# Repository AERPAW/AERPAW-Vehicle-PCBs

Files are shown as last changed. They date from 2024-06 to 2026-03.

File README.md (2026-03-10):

# vehicle-pcbs

PCB design files for vehicles and accessories used by AERPAW project.

Designs:

- `LAM-original` contains projects (carrier, PDB) for original LAM revisions (<2025)
- `LAM-simplified` contains updated PDB (power distribution board) (>2025)
- `LightBoard` contains design for auxilary LED drivers for SAM revisions
- `SAM4-old` contains projects for original SAM revisions carrier (<2026)
- `SAME` contains projects for updated SAM revisions

Util:

- `kicad-libs` is a unified symbol/footprint library for all projects. Configure future projects to point at this!

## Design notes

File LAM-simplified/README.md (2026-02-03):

# LAM PCBs

This contains various revisions of LAM PDB (power distribution board) PCBs.

`r1.3` is the suggested revision for older LAM hexarotors.

`r2.0` is the suggested revision for newer HAM-based designs, as it supports higher current capacity (at the cost of a different mechanical footprint from 1.X).

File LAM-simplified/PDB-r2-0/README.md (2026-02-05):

# HAM PDBs

This directory contains the KiCad (9.X) project files with design and manufacturing details for the HAM PDB (power distribution board)s.

The PDB ingests raw battery voltage and provides connectors for peripherals to hook into this net.

- 4x 2x3 2.54mm male -- to (original) carrier board
- 2x XT30 -- to aux systems
- 6x XT60 -- to motors
- 2x AS150 -- to batteries (use parallel connection)

The board also has access to a regulated 5V rail from the carrier board.
This net is currently unused, but left in for future revisions that might make use of it.

## Manufacturing

The `jlcpcb` directory and `jlcpcb.zip` contains manufacturing files that can be directly uploaded to JLCPCB's website.
A handful of settings should be changed: pick a copper weight >= 3oz, and as high of a temperature substrate as available.
The below screenshot shows an example order that should be reasonable for this application.

Screenshot 2026-02-05 at 13-56-46 Online PCB Instant Quote - JLCPCB

Assembly of this board is simple: just solder through-hole connectors into their appropriate slots.
Do not directly solder wires into this PCB.
Every connection must be made through a connector to ensure that all current expectations on wires/connectors are upheld.

When mechanically attaching this board inside the drone chassis, use brass standoffs.
The board, by design, exposes the GND net to all mechanical mounting holes.
This *should* aid with grounding the drone's chassis dependent on the rest of the mechanical design.

## BOM

A BOM can be assembled by looking at the LCSC field.
Each part number can be searched on LCSC to get ordering information and/or search terms to find similar parts.
LCSC is preferred in this case because they are the only major parts provider sourcing the needed AMASS connectors, and their system is tightly integrated with JLC.

- [2x XT30-F](https://www.lcsc.com/product-detail/C2913282.html)
- [6x XT60-F](https://www.lcsc.com/product-detail/C428722.html)
- [2x AS150UPW-M](https://www.lcsc.com/product-detail/C19268054.html)
- ?x standard 2.54mm pin headers
- [3x Keystone 5010 test points (optional)](https://www.lcsc.com/product-detail/C2906765.html)

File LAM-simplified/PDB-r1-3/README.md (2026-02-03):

# "EASYLAM" PDB (revision 1.3)

This directory contains the KiCad (9.X) project files with design and manufacturing details for the simplified LAM PDB (power distribution board)s.

The PDB ingests raw battery voltage and provides connectors for peripherals to hook into this net.

- 4x 2x3 2.54mm male -- to carrier board
- 2x XT30 -- to aux systems
- 6x XT60 -- to motors
- 2x XT90 -- to batteries (use parallel connection to batteries)

There isn't a strict upper limit on the current that our drones might demand, but this board is fairly conservatively designed to help move failure points to offboard connectors.

The board also has access to a regulated 5V rail from the carrier board.
This net is currently unused, but left in for future revisions that might make use of it.

## Manufacturing

The `jlcpcb` directory contains manufacturing files that can be directly uploaded to JLCPCB's website.
A handful of settings should be changed, documented below:

- screenshot TODO, but we want to pick the heaviest copper weight available and an appropriate process for exposed pads (ENIG?)

Assembly of this board is simple: just solder through-hole connectors into their appropriate slots.
Do not directly solder wires into this PCB.
Every connection must be made through a connector to ensure that all current expectations on wires/connectors are upheld.

When mechanically attaching this board inside the drone chassis, use brass standoffs.
The board, by design, exposes the GND net to all mechanical mounting holes.
This *should* aid with grounding the drone's chassis dependent on the rest of the mechanical design.

## BOM

A BOM can be assembled by looking at the LCSC field.
Each part number can be searched on LCSC to get ordering information and/or search terms to find similar parts.
LCSC is preferred in this case because they are the only major parts provider sourcing the needed AMASS connectors, and their system is tightly integrated with JLC.

For simplicity, a BOM is below:

- [2x XT30-F](https://www.lcsc.com/product-detail/C2913282.html)
- [6x XT60-F](https://www.lcsc.com/product-detail/C428722.html)
- [2x XT90-F](https://www.lcsc.com/product-detail/C3040690.html)
- ?x standard 2.54mm pin headers
- [3x Keystone 5010 test points (optional)](https://www.lcsc.com/product-detail/C2906765.html)

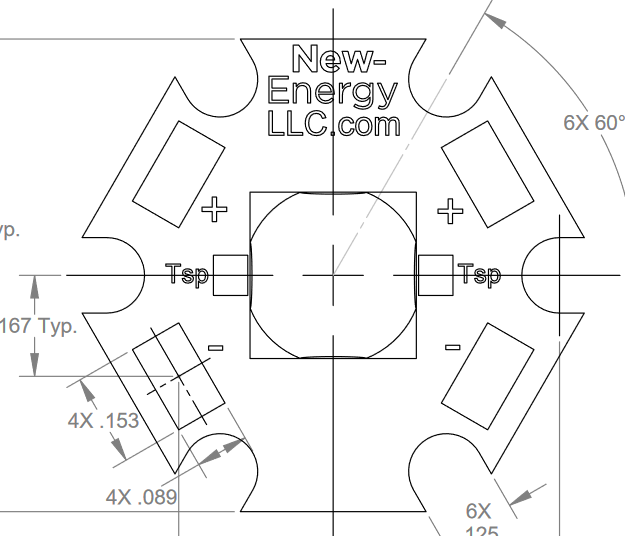
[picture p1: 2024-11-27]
LightBoard/starboard_profile.png

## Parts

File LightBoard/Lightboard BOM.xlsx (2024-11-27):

Reference | Part | Footprint | Qty | Link | Price (1) | Price (total) | Misc
C1 | Cap 0.1u | 1206 | 1 | https://www.digikey.com/en/products/detail/vishay-sprague/293D104X9035A2TE3/1559461 | $0.43 | $0.43 | Decoupling (tantalum)
J1, J2 | JST_EH 2x2.5mm Male Horiz |  | 2 | https://www.digikey.com/en/products/detail/jst-sales-america-inc/S2B-EH/926533?0=%2Fheaders-male-pins | $0.12 | $0.24 | Rated for 3A
R1, R2, R4, R5, R8 | Res 10k | 1206 | 5 | https://www.digikey.com/en/products/detail/yageo/RC1206FR-0710KL/728483 | $0.10 | $0.50
R3 | Res 0.22 1% | 1206 | 1 | https://www.digikey.com/en/products/detail/eaton-electronics-division/MFHA1206R2200FC/16713417 | $0.34 | $0.34 | Current tuning
R6 | Res 80k | 1206 | 1 | https://www.digikey.com/en/products/detail/yageo/RC1206FR-0780K6L/729126 | $0.10 | $0.75
R7 | Res 35 0.5W | 1206 | 1 | https://www.digikey.com/en/products/detail/yageo/SR1206JR-7T36RL/9696427 | $0.75 | $0.75 | Power shunt (optional)
U1 | IS32LT3140A | 14-TSSOP | 1 | https://www.digikey.com/en/products/detail/lumissil-microsystems/IS32LT3140A-ZLA3-TR/15194878 | $2.00 | $2.00 | LED Driver
Heat Sink |  |  | 1 | https://www.digikey.com/en/products/detail/sparkfun-electronics/PRT-18704/21443080 | $2.44 | $2.44 | Optional
M3 Standoff |  |  | 6 | https://www.digikey.com/en/products/detail/keystone-electronics/24339/1532140 | $0.91 | $5.46
PCB |  |  | 1 |  | $0.40 | $0.40 | JLCPCB
 |  |  |  |  |  | $13.31

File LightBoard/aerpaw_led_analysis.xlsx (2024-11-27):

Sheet: Sheet1
LED | Link | Color | Brightness (lm/W) | Brightness (80%) | V_f | Current (max) | Power (80%) | Price | Power (80%) | Brightness (80%)
MHBBWT | https://www.digikey.com/en/products/detail/new-energy/MHBBWT-0000-000C0BE265E-SB01/6817726 | 6500K | 146 | 715.4 | 8.75 | 0.7 | 4.9 | 6.24 | 4.9 | 715.4
BXRC-40C1001 | https://www.digikey.com/en/products/detail/bridgelux/BXRC-40C1001-C-83/15520071 | 4000K | 192 | 4715.52 | 30.7 | 1 | 24.56 | 7.1 | 24.56 | 4715.52
BXRC-40E1000 | https://www.digikey.com/en/products/detail/bridgelux/BXRC-40E1000-D-83/12313698 | 4000K | 182 | 3625.44 | 24.9 | 1 | 19.92 | 4.78 | 19.92 | 3625.44
XHP70B | https://www.digikey.com/en/products/detail/new-energy/XHP70B-00-0000-0D0BP250E-SB01/7428211 | 5000k | 151 | 3479.04 | 12 | 2.4 | 23.04 | 20.5 | 23.04 | 3479.04
LZ4-40C | https://www.digikey.com/en/products/detail/ams-osram-usa-inc/LZ4-40CW08-0065/4970100 | 6500K | 101 | 1018.08 | 12.6 | 1 | 10.08 | 16.5 | 10.08 | 1018.08
MHBBWT-0000 | https://www.digikey.com/en/products/detail/new-energy/MHBBWT-0000-000C0HC427G-SB01/6817724 | 2700K | 117 | 573.3 | 8.75 | 0.7 | 4.9 | 6.69 | 4.9 | 573.3
LST1-01 | https://www.digikey.com/en/products/detail/new-energy/LST1-01C54-5765-01/16679676 | 5700K | 116 | 1108.032 | 3.98 | 3 | 9.552 | 10.24 | 9.552 | 1108.032
LST1-01G03 | https://www.digikey.com/en/products/detail/new-energy/LST1-01G03-5070-01/9816713 | 5000K | 114 | 902.88 | 3.3 | 3 | 7.92 | 4.28 | 7.92 | 902.88
 |  |  |  |  |  |  |  |  | 8 | 520
 |  |  |  |  |  |  |  |  | 1.68 | 82.32
LZ4-40R108-0000 | https://www.digikey.com/en/products/detail/ams-osram-usa-inc/LZ4-40R108-0000/4976731 | red | 65 | 520 | 10 | 1 | 8 | 13.91 | 2.706 | 365.31
LST1-01H06-RED1-01 | https://www.digikey.com/en/products/detail/new-energy/LST1-01H06-RED1-01/10663117 | red | 49 | 82.32 | 2 | 1.05 | 1.68 | 4.22
 |  |  |  |  |  |  |  |  | 2.562 | 299.754
LST1-01H06-LME1-01 | https://www.digikey.com/en/products/detail/new-energy/LST1-01H06-LME1-01/10663113 | lime | 135 | 365.31 | 2.75 | 1.23 | 2.706 | 5.72
LST1-01H07-GRN1-01 | https://www.digikey.com/en/products/detail/new-energy/LST1-01H07-GRN1-01/10663119 | green | 117 | 299.754 | 3.05 | 1.05 | 2.562 | 4.22

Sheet: bom
3mm standoffs
jst-eh headers (2 pin)

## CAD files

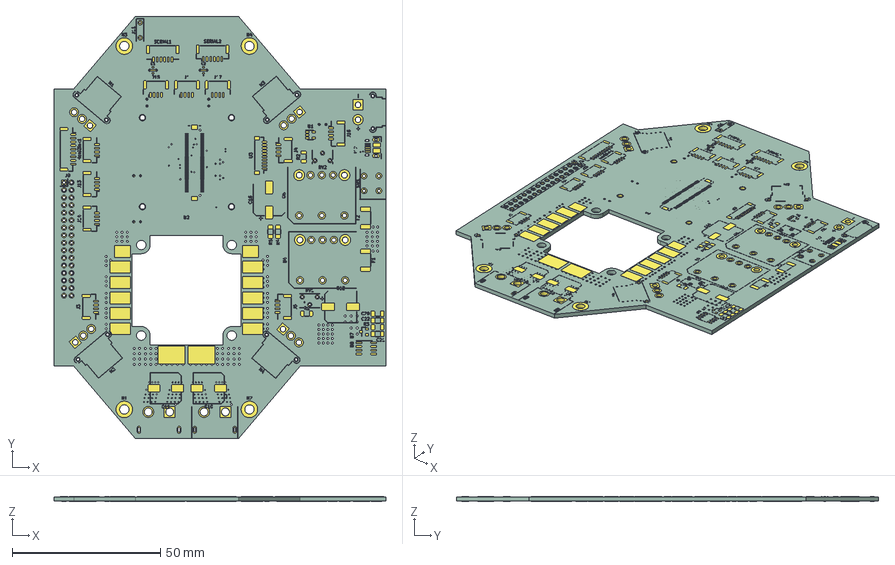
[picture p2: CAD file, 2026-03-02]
SAM-original/SAM4_Mainboard.step
111.7 x 142.2 x 1.66 mm
SAM4_Mainboard_pad
SAM4_Mainboard_silkscreen x 2
SAM4_Mainboard_PCB

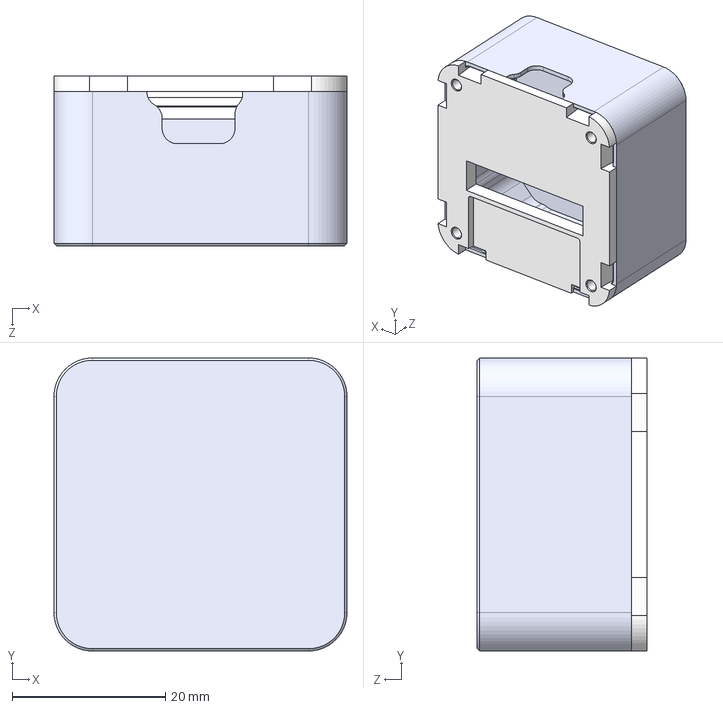
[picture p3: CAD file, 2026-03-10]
kicad-libs/3d/Cube.STEP
38.2 x 38.2 x 22.1 mm
cubemini_base_v1_20180513.stp
std_cube_lid_h20-1mm_20180816.stp

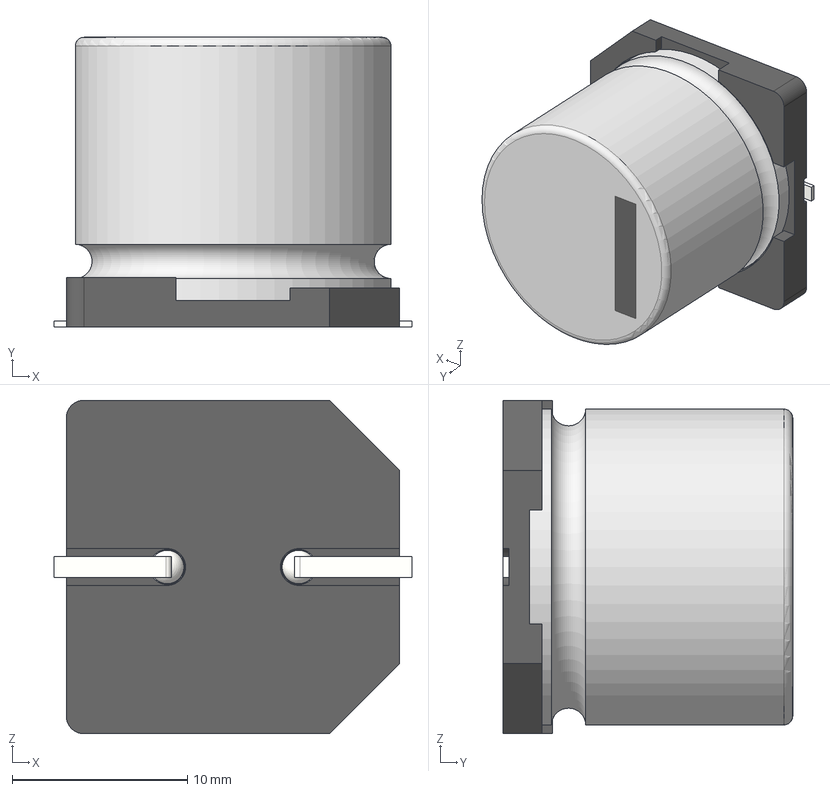
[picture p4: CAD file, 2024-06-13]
LAM-original/P2_PowerSystem/18 SIZE CODE K16.stp
20.4 x 16.5 x 19.0 mm
標準品ケースΦ18x15L SIDE CODE K1 6
標準品座版Φ18 SIZE CODE K16
標準品リード線Φ18 SIZE CODE K1 6 x 2

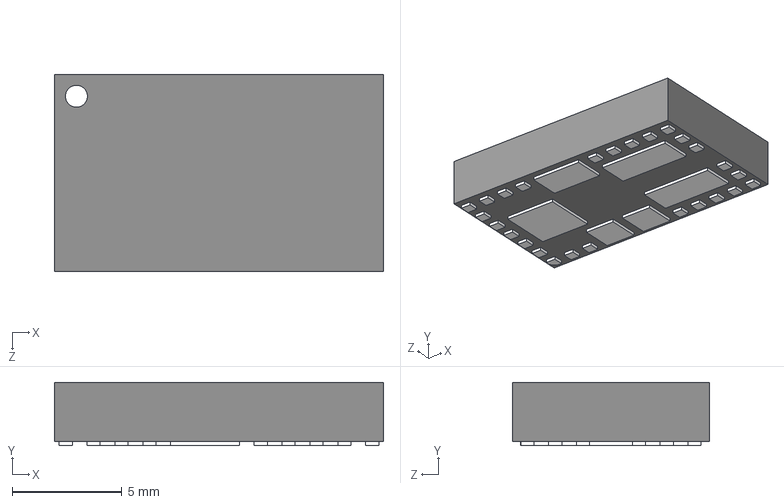
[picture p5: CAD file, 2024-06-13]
LAM-original/P2_PowerSystem/2020-09-24_06-53-47/21-0879B_L32915+3.STEP
15.0 x 2.88 x 9.00 mm

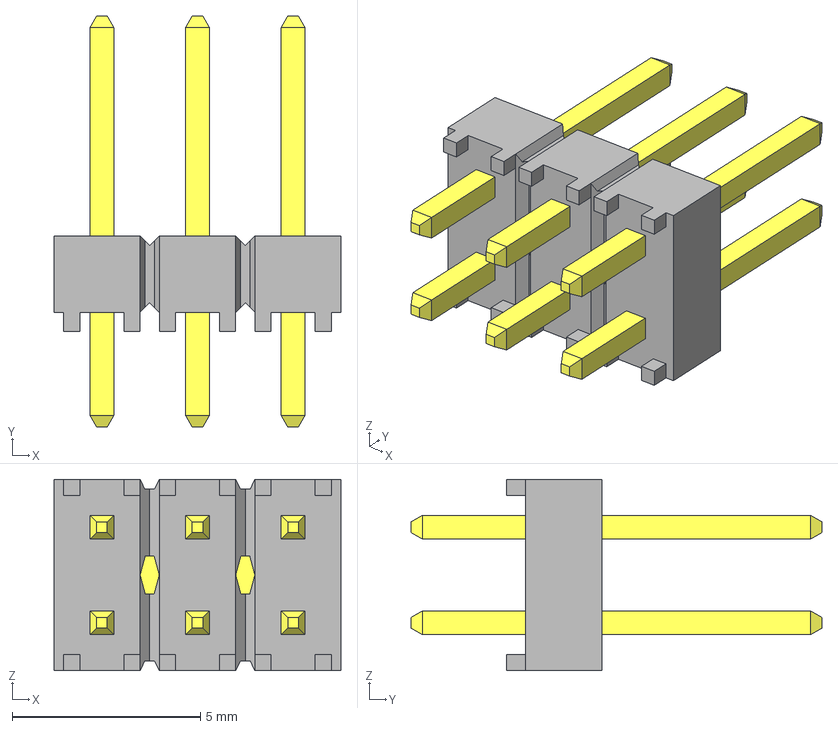
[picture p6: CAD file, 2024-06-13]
LAM-original/P2_PowerSystem/PDB/TSW-103-07-F-D.stp
7.62 x 10.9 x 5.08 mm
_TSW-103-07-F-D_body
_T-1S6-07-TSW-1-07-3-D

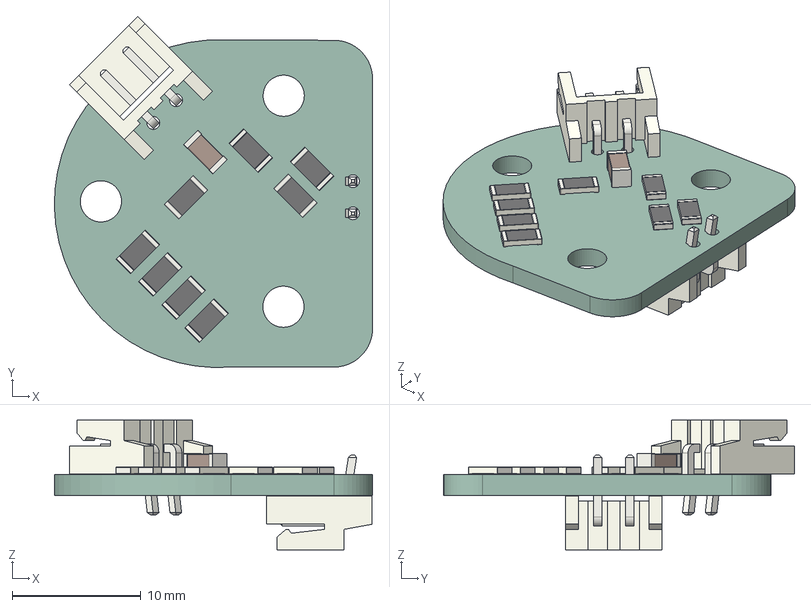
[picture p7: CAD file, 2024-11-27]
LightBoard/lightboard/lightboard.step
24.7 x 27.3 x 10.1 mm
R_1206_3216Metric x 8
JST_S2B_EH x 2
C_1206_3216Metric
lightboard_PCB

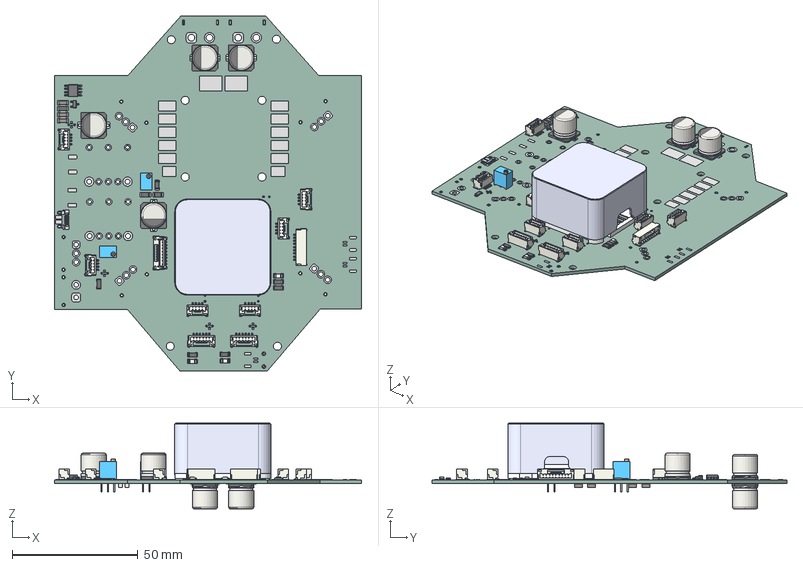
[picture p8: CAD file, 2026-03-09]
SAM-original/sam4_r1.2.step
122.0 x 141.0 x 34.1 mm
R_1206_3216Metric x 9
JST_GH_SM09B-GHS-TB_1x09-1MP_P1.25mm_Horizontal
CP_Elec_10x10 x 4
C_1206_3216Metric x 11
SOIC-8_3.9x4.9mm_P1.27mm
JST_GH_BM04B-GHS-TBT_1x04-1MP_P1.25mm_Vertical x 6
CP_Elec_10x10.5 x 2
JST_SH_BM10B-SRSS-TB_1x10-1MP_P1.00mm_Vertical
LED_1206_3216Metric x 3
Potentiometer_Bourns_3266W_Vertical x 2
JST_GH_BM08B-GHS-TBT_1x08-1MP_P1.25mm_Vertical
JST_GH_BM06B-GHS-TBT_1x06-1MP_P1.25mm_Vertical x 2
SOT-23
cubemini_base_v1_20180513.stp
std_cube_lid_h20-1mm_20180816.stp
sam4_pad
sam4_PCB

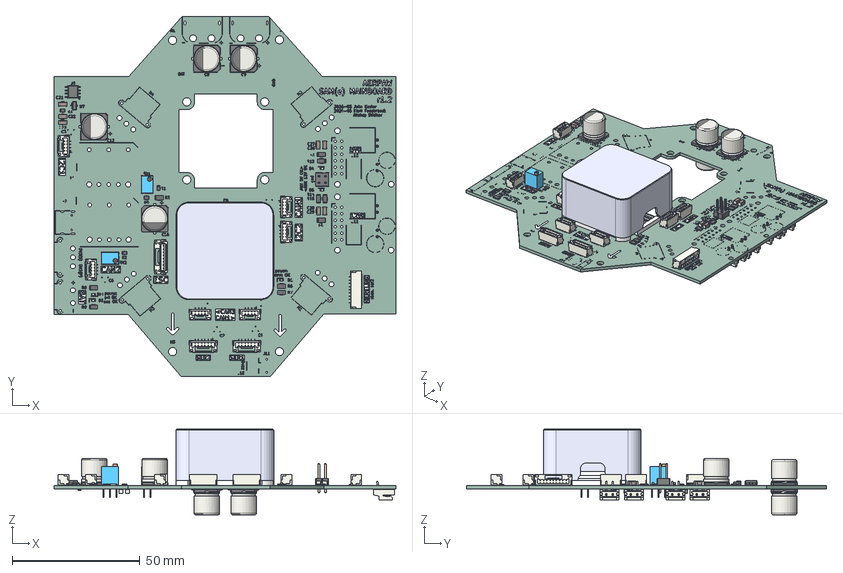
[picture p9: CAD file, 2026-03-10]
SAME/sam4/sam4.step
133.8 x 141.0 x 33.6 mm
LED_0603_1608Metric x 5
R_0805_2012Metric x 6
JST_GH_SM09B-GHS-TB_1x09-1MP_P1.25mm_Horizontal
CP_Elec_10x10 x 4
R_1206_3216Metric x 8
C_1206_3216Metric x 15
Fuse_1206_3216Metric x 2
SOIC-8_3.9x4.9mm_P1.27mm
JST_GH_BM04B-GHS-TBT_1x04-1MP_P1.25mm_Vertical x 6
CP_Elec_10x10.5 x 2
JST_SH_BM10B-SRSS-TB_1x10-1MP_P1.00mm_Vertical
PinHeader_2x02_P2.54mm_Vertical
Potentiometer_Bourns_3266W_Vertical x 2
JST_GH_BM08B-GHS-TBT_1x08-1MP_P1.25mm_Vertical
JST_GH_BM06B-GHS-TBT_1x06-1MP_P1.25mm_Vertical x 2
SOT-23
cubemini_base_v1_20180513.stp
std_cube_lid_h20-1mm_20180816.stp
JST_EH_S2B-EH_1x02_P2.50mm_Horizontal x 4
sam4_silkscreen x 2
sam4_PCB

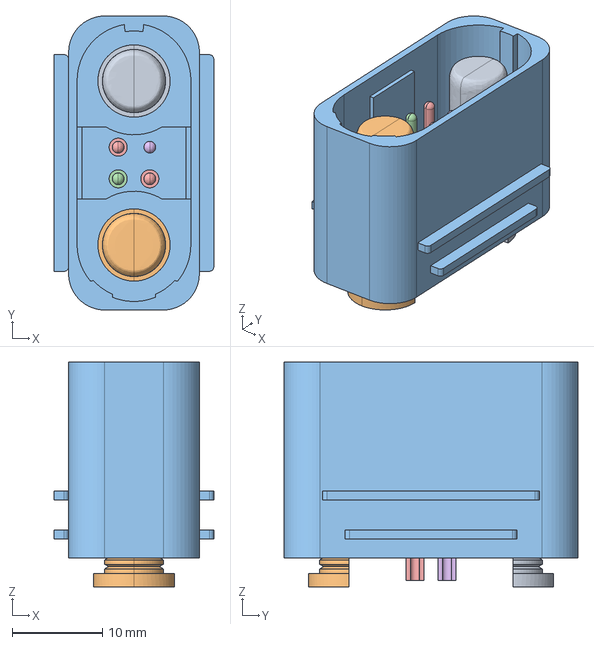
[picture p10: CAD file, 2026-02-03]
kicad-libs/3d/Amass AS150U Anti Spark Connector.stp
17.7 x 32.6 x 24.9 mm

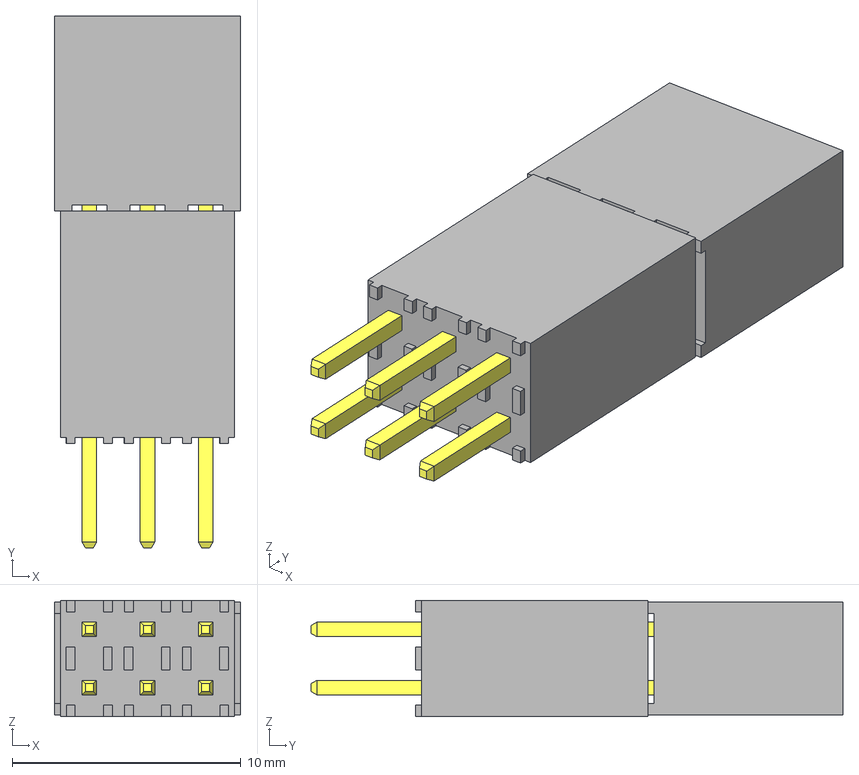
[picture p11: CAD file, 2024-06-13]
LAM-original/P2_PowerSystem/ESQ-103-44-L-D.stp
8.13 x 23.2 x 5.08 mm
_ESQ-103-44-L-D_socket
_ESQ-103-44-L-D_pins
_ESQ-103-44-G-D-LL_bpins

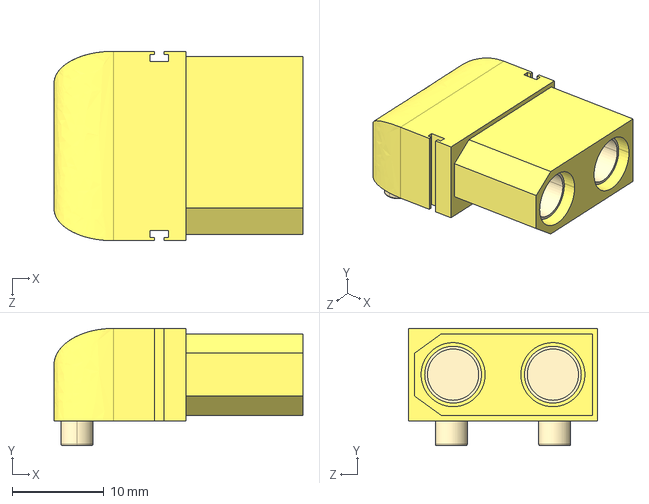
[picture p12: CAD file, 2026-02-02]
kicad-libs/3d/XT90PW-F.STEP
27.2 x 12.8 x 20.7 mm

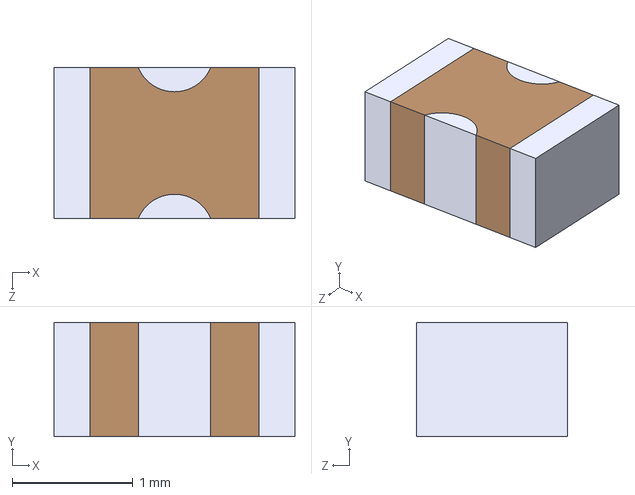
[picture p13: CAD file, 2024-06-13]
LAM-original/P2_PowerSystem/NFM21HC224R1A3D.step
2.00 x 0.95 x 1.25 mm

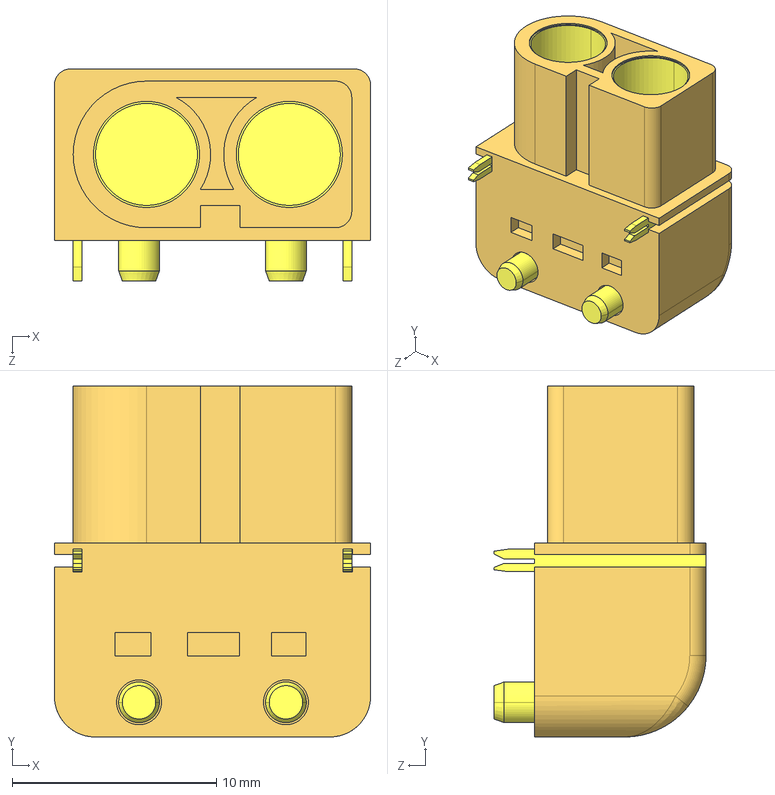
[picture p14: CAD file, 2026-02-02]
kicad-libs/3d/XT60PW-F.STEP
15.5 x 17.2 x 10.4 mm

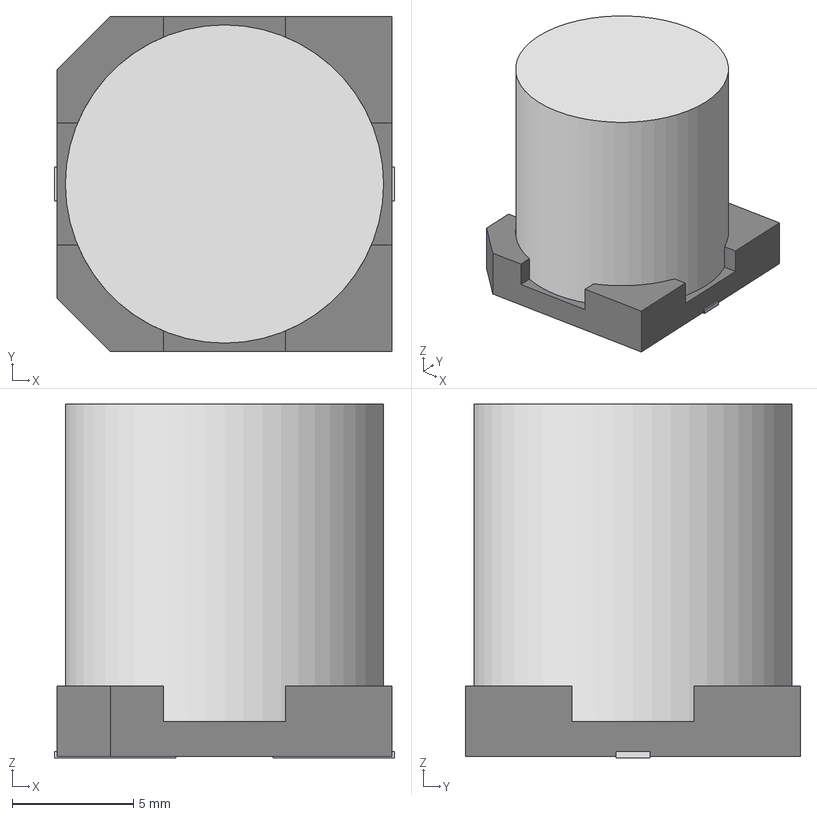
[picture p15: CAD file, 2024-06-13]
LAM-original/P2_PowerSystem/PCAP_12_5x13_5-ELECT_NCA.step
14.0 x 13.8 x 14.6 mm

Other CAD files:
kicad-libs/3d/XT90PW-M.STEP
LAM-original/P2_PowerSystem/herelink_footprint.dxf
kicad-libs/3d/XT30PW-F.STEP
LAM-original/P2_PowerSystem/XT-60_Macho 1.STEP
LAM-original/P2_PowerSystem/0678H9150-02.step
LAM-original/P2_PowerSystem/Buzzer - Peak-Peak, Single Tone 4.8kHz Piezo 1 ~ 15V 90dB 4.8V, PT-2404.STEP
LAM-original/P2_PowerSystem/PSM.STEP
LAM-original/P2_PowerSystem/SFC-120-T2-F-D-A.stp
LAM-original/P2_PowerSystem/SSQ-103-02-G-D.stp

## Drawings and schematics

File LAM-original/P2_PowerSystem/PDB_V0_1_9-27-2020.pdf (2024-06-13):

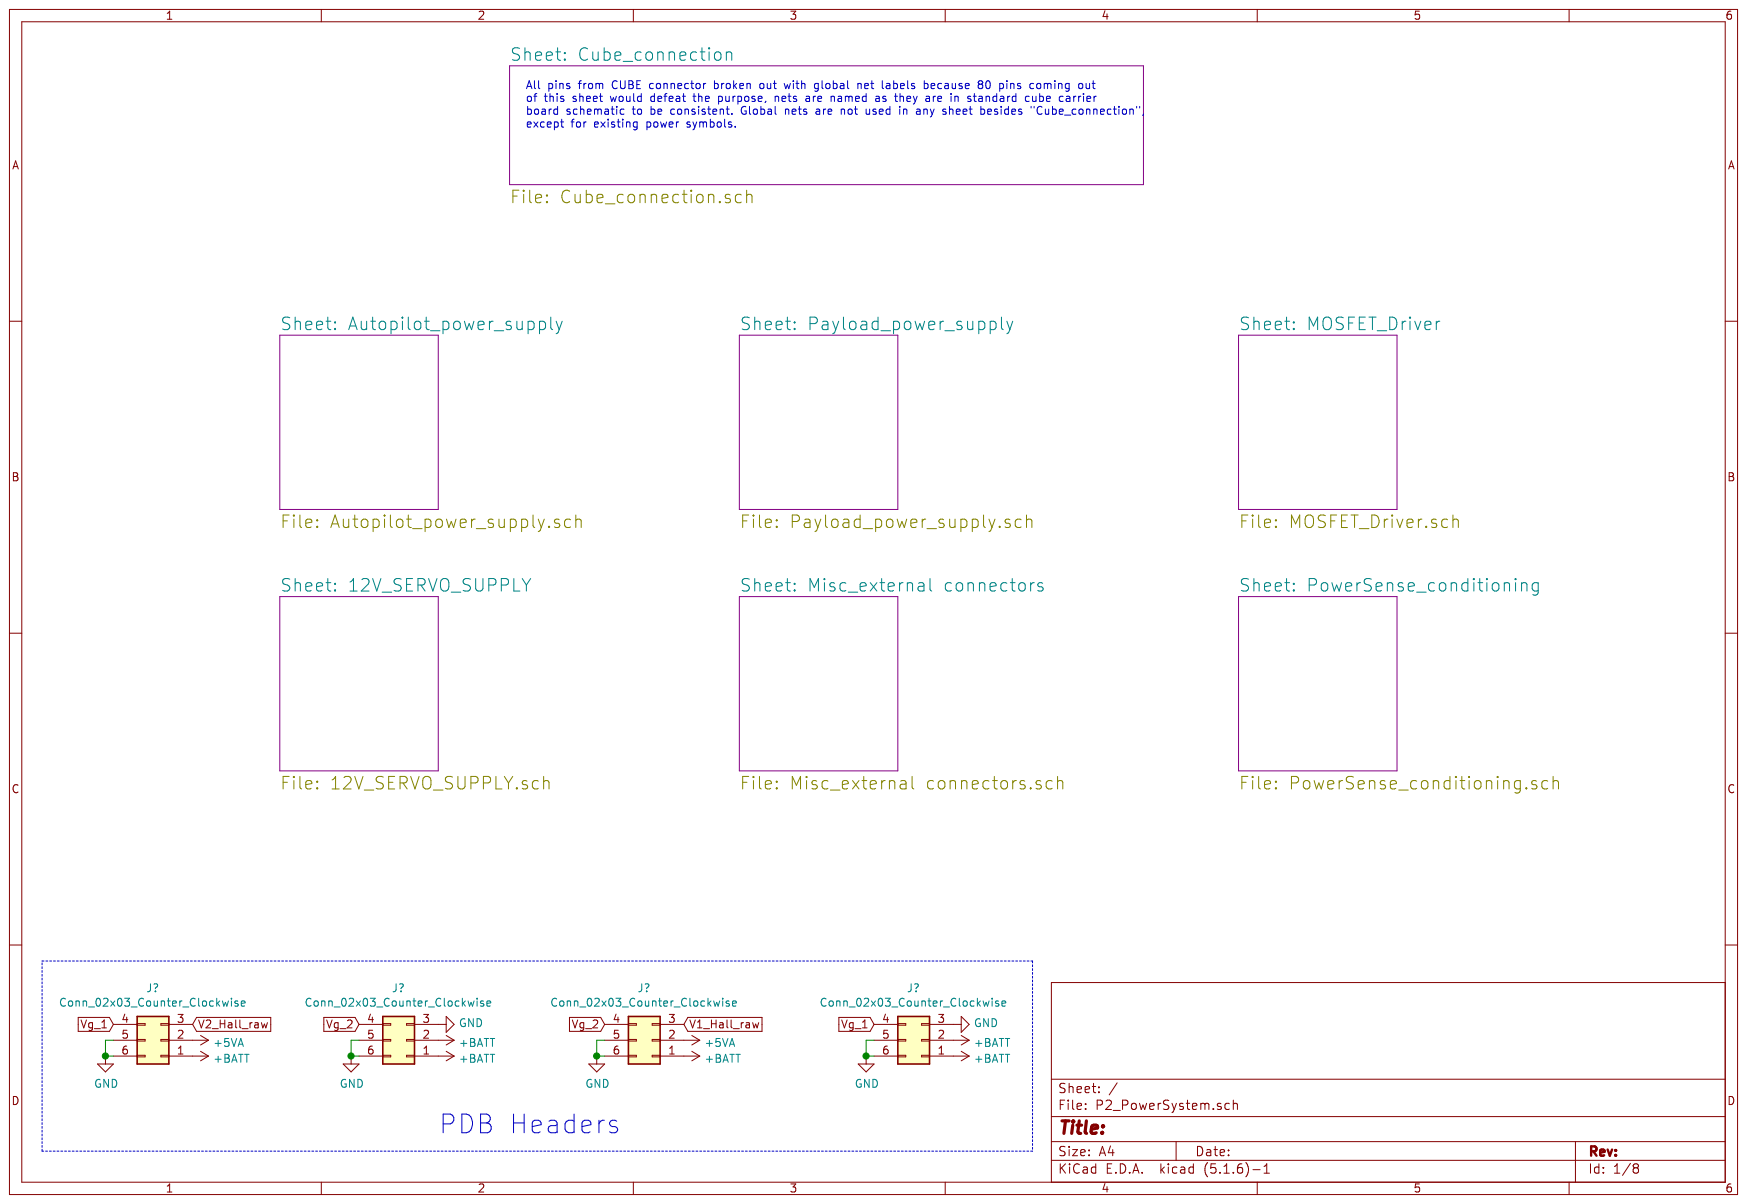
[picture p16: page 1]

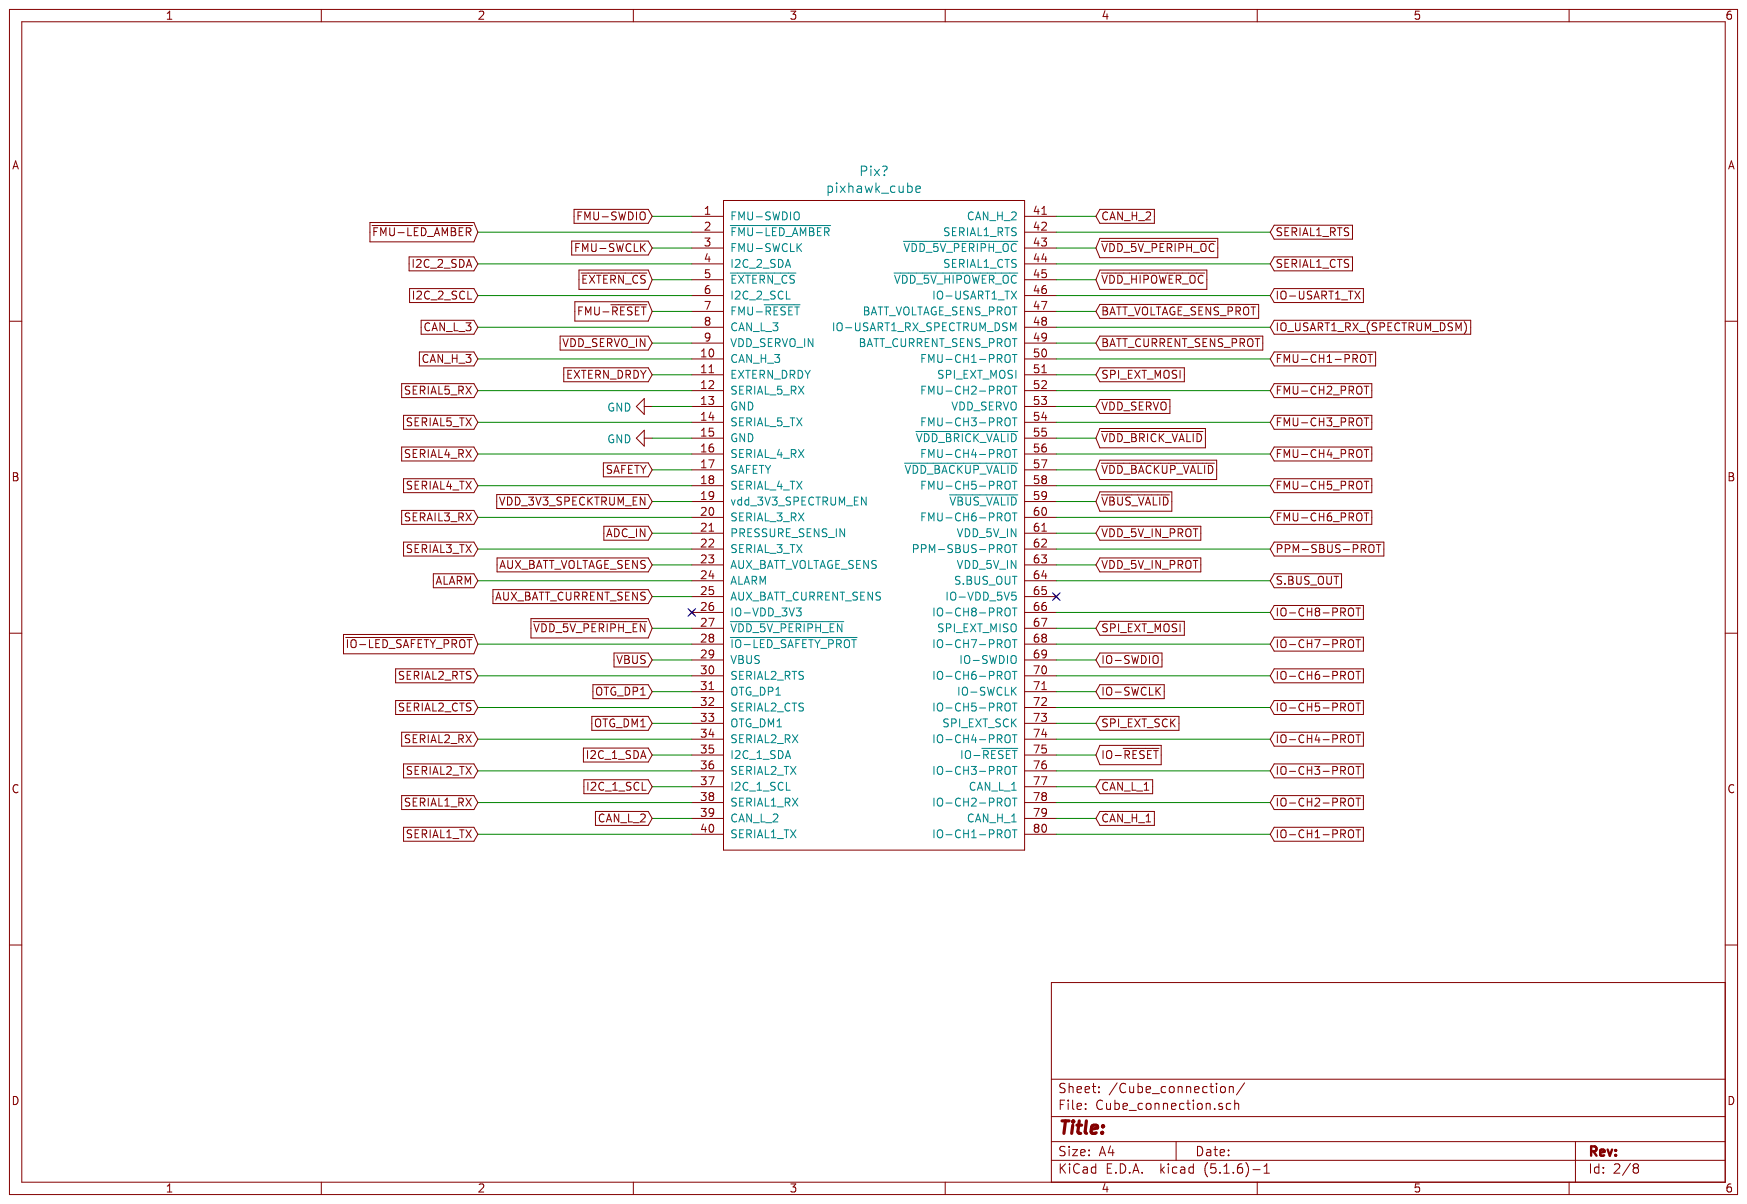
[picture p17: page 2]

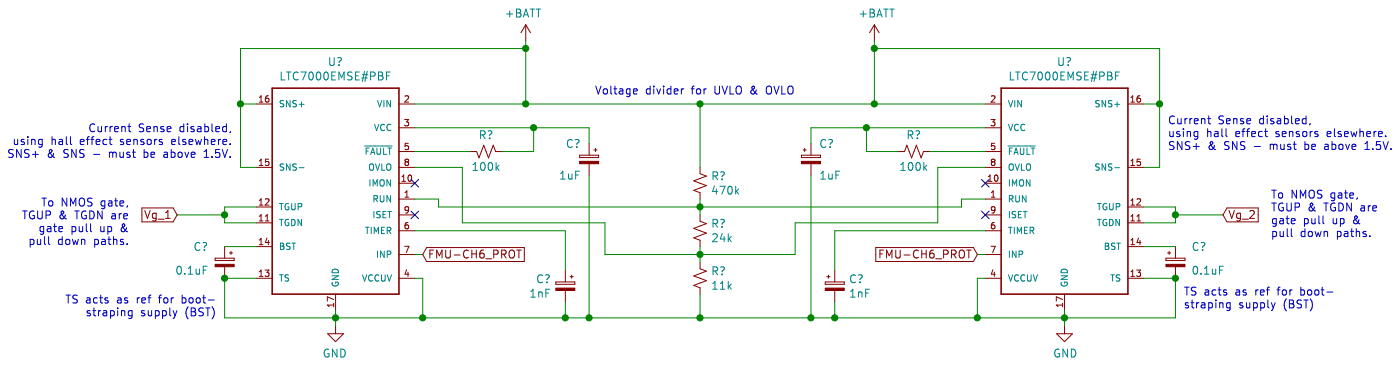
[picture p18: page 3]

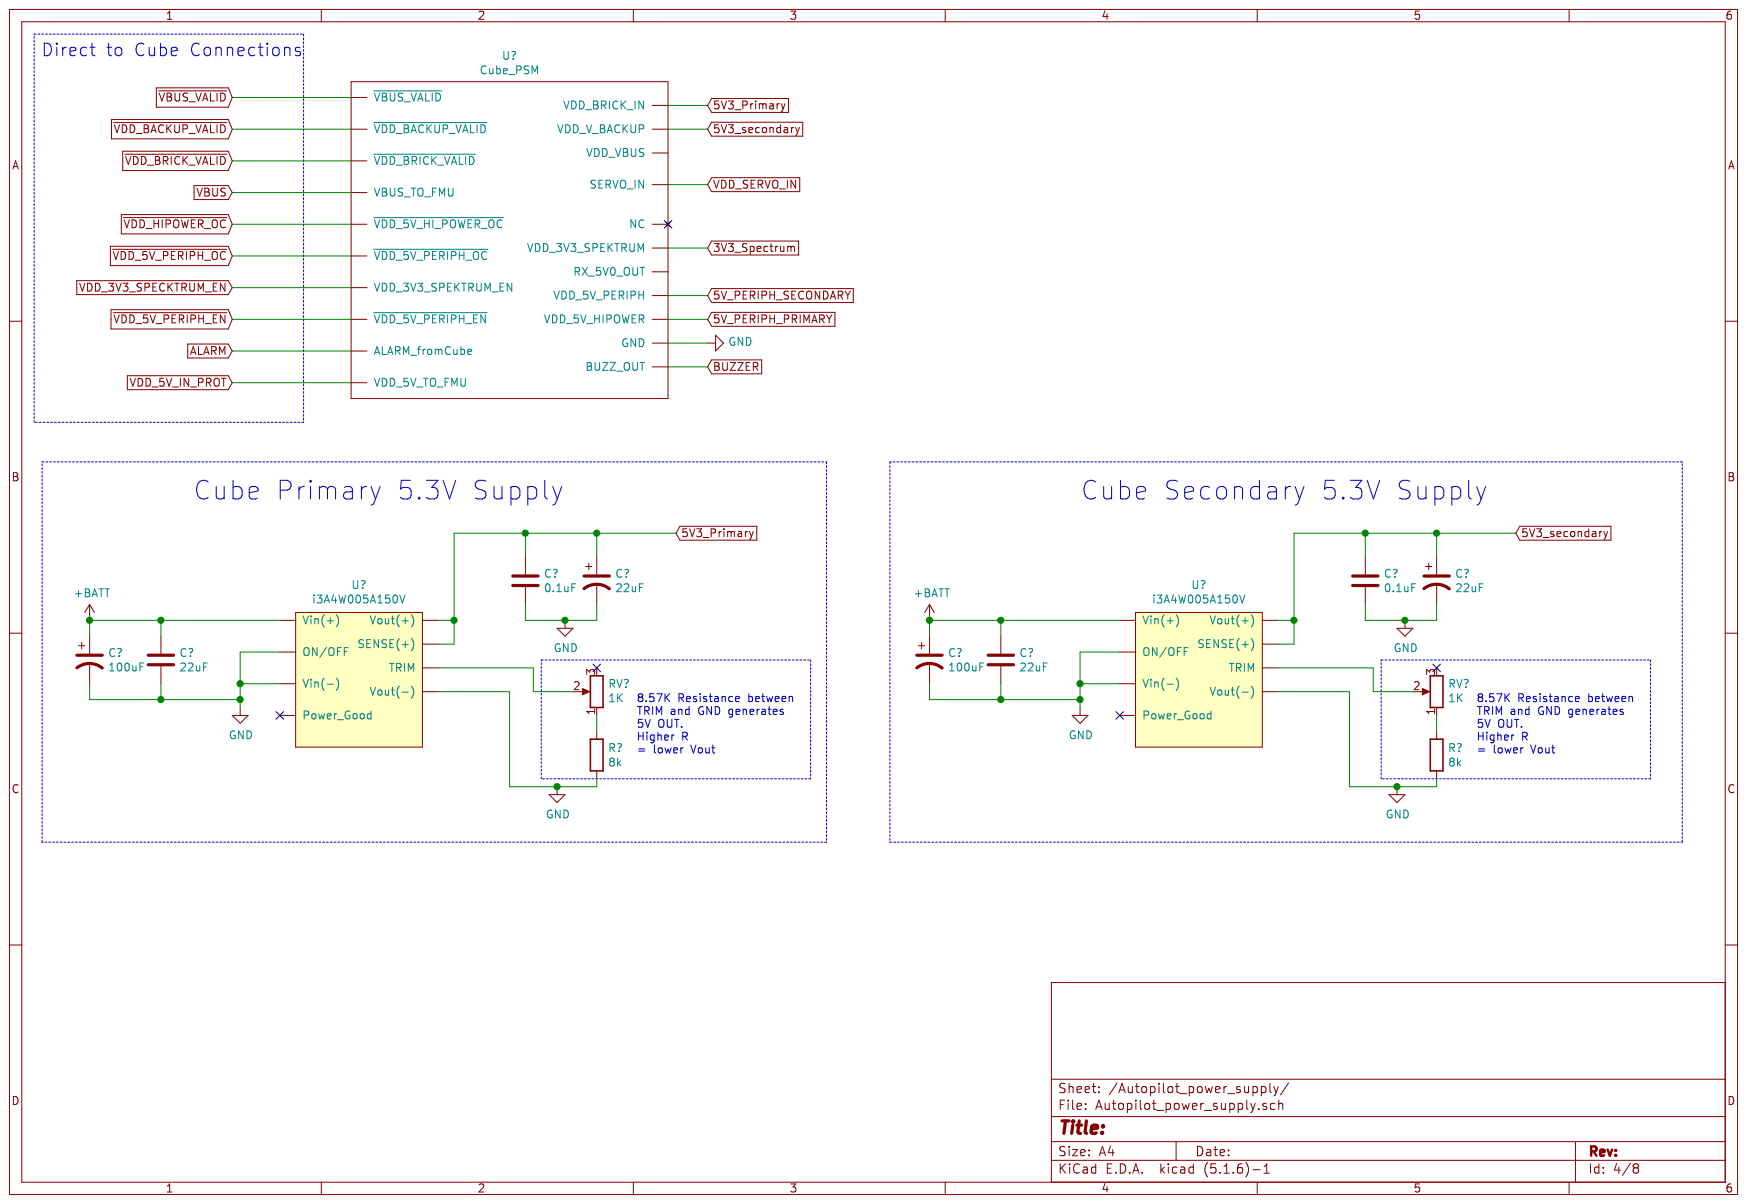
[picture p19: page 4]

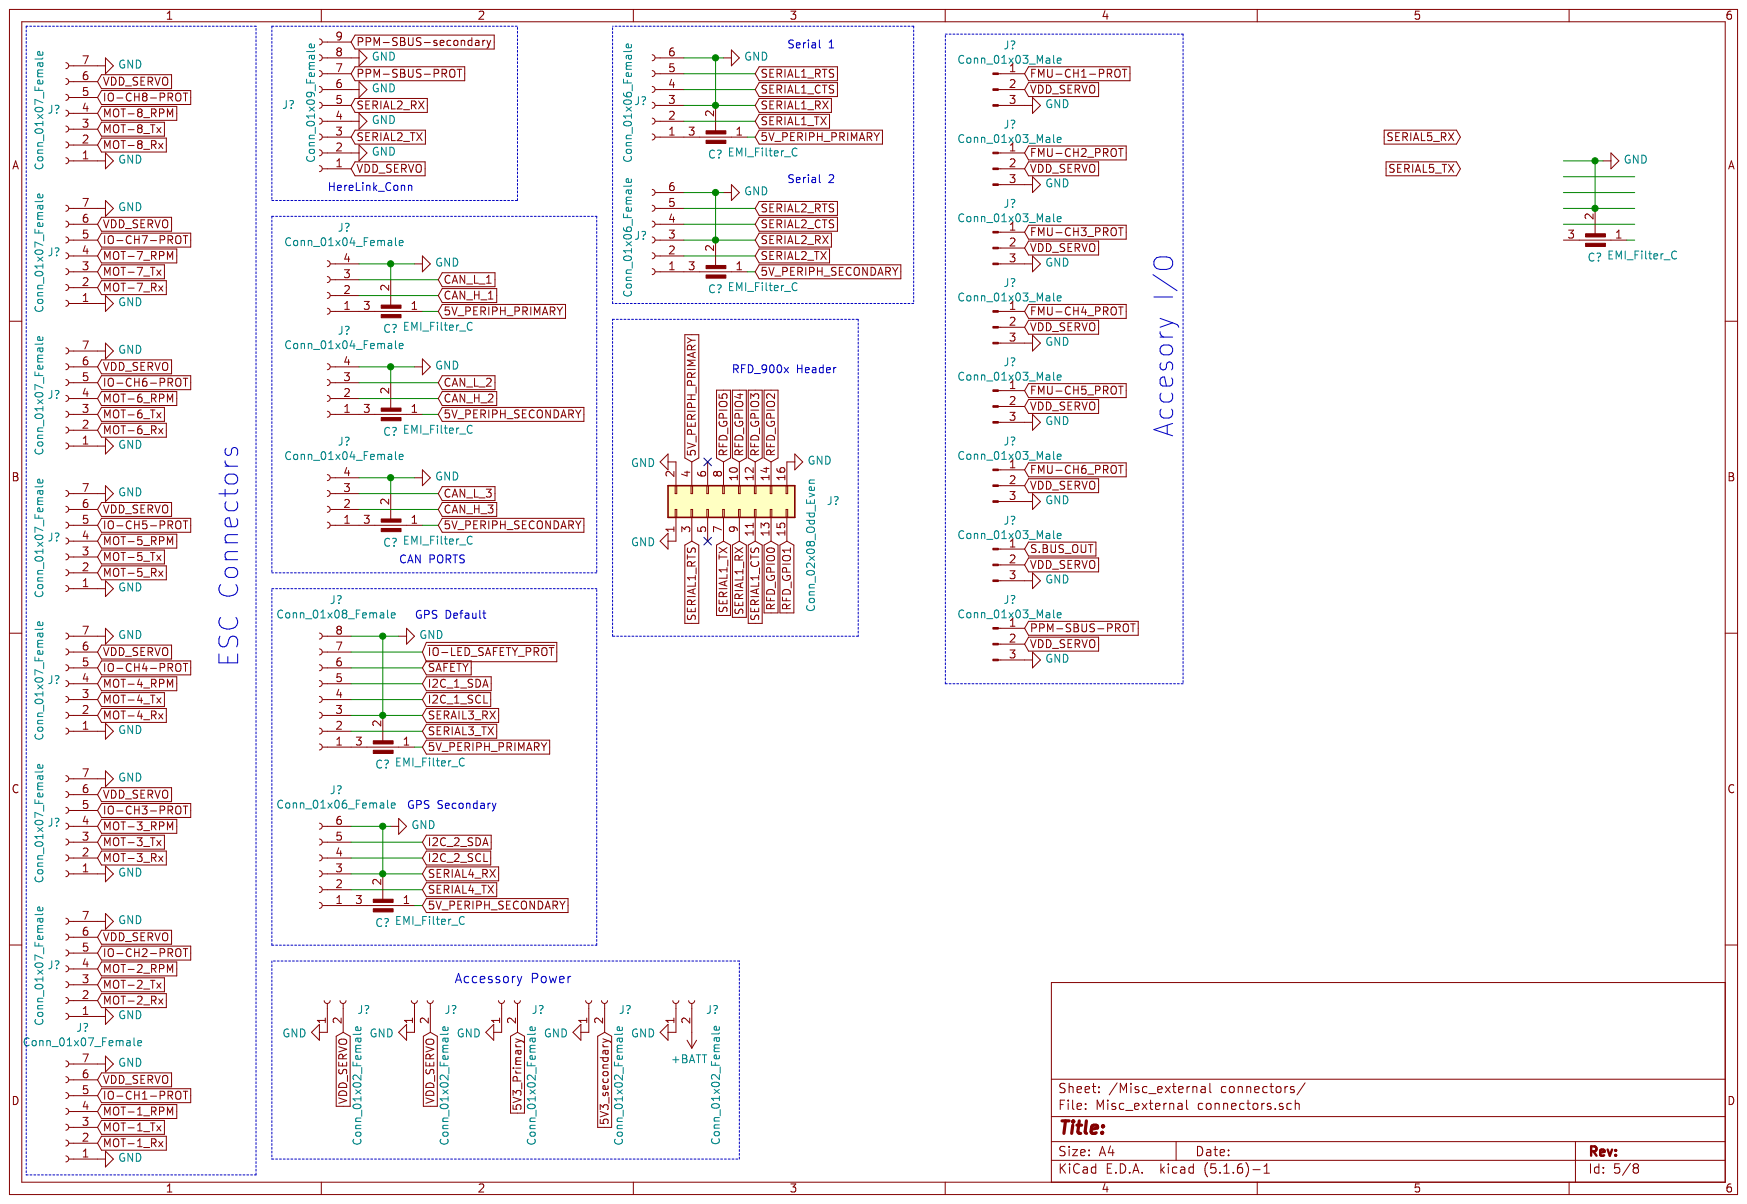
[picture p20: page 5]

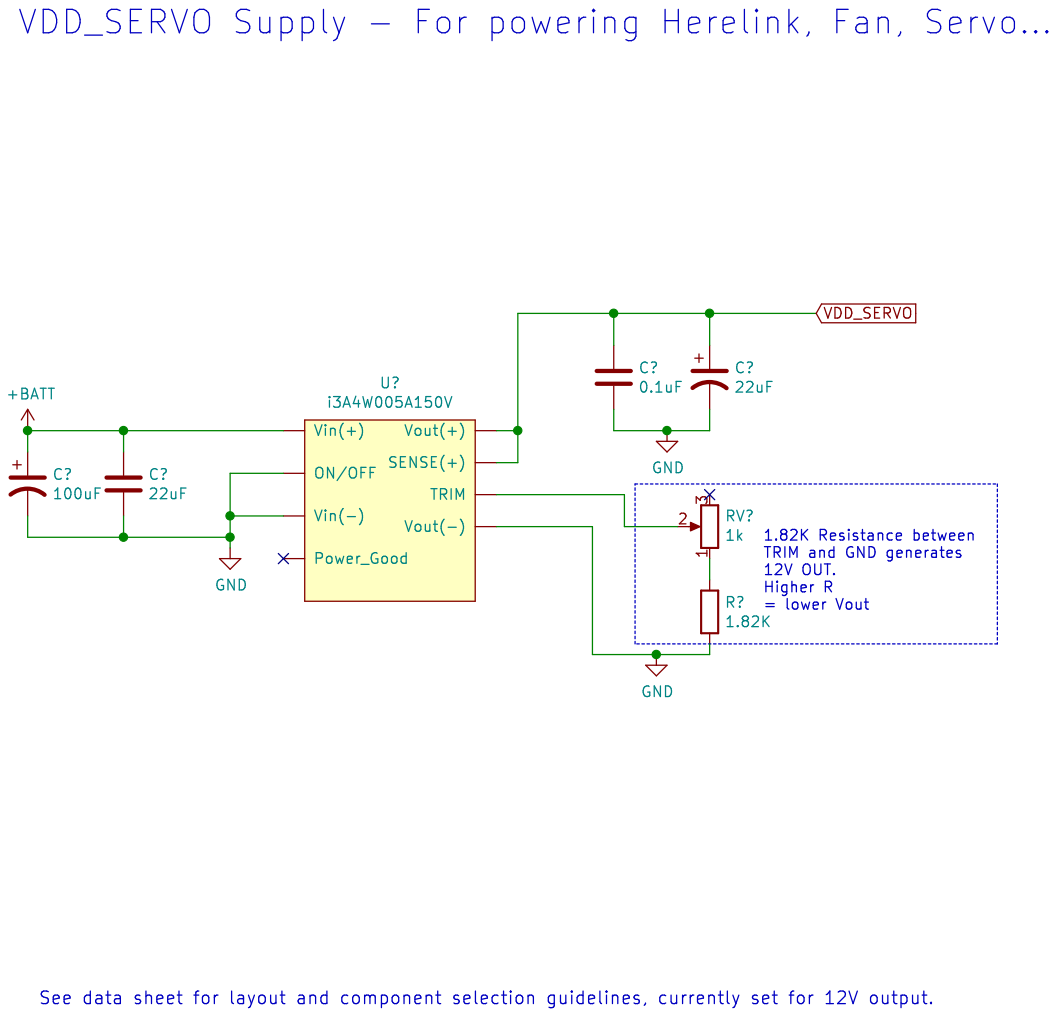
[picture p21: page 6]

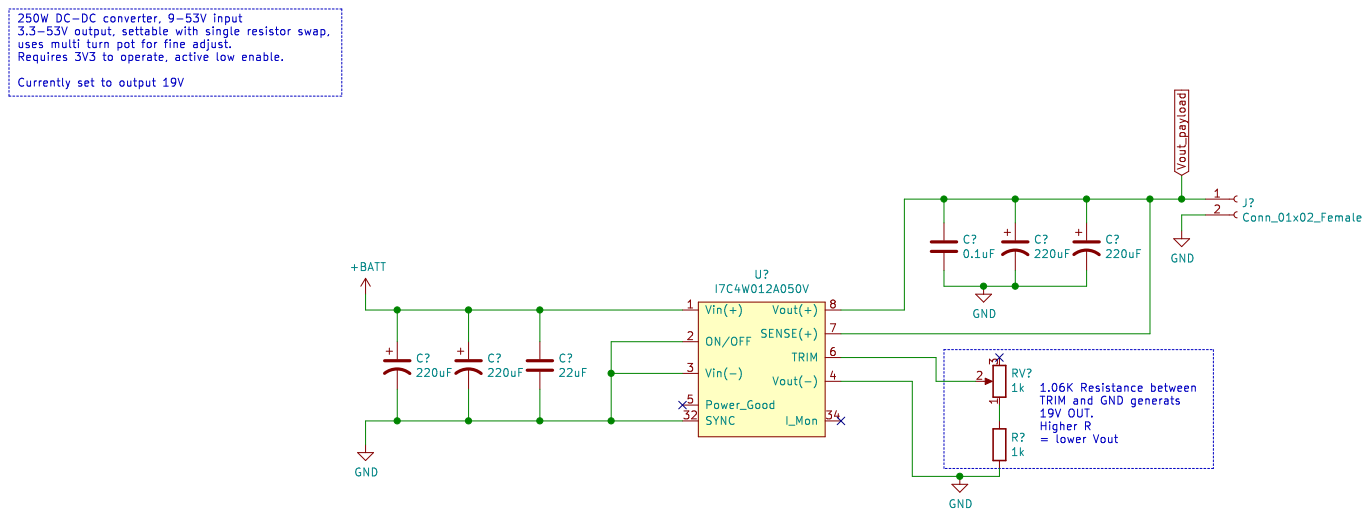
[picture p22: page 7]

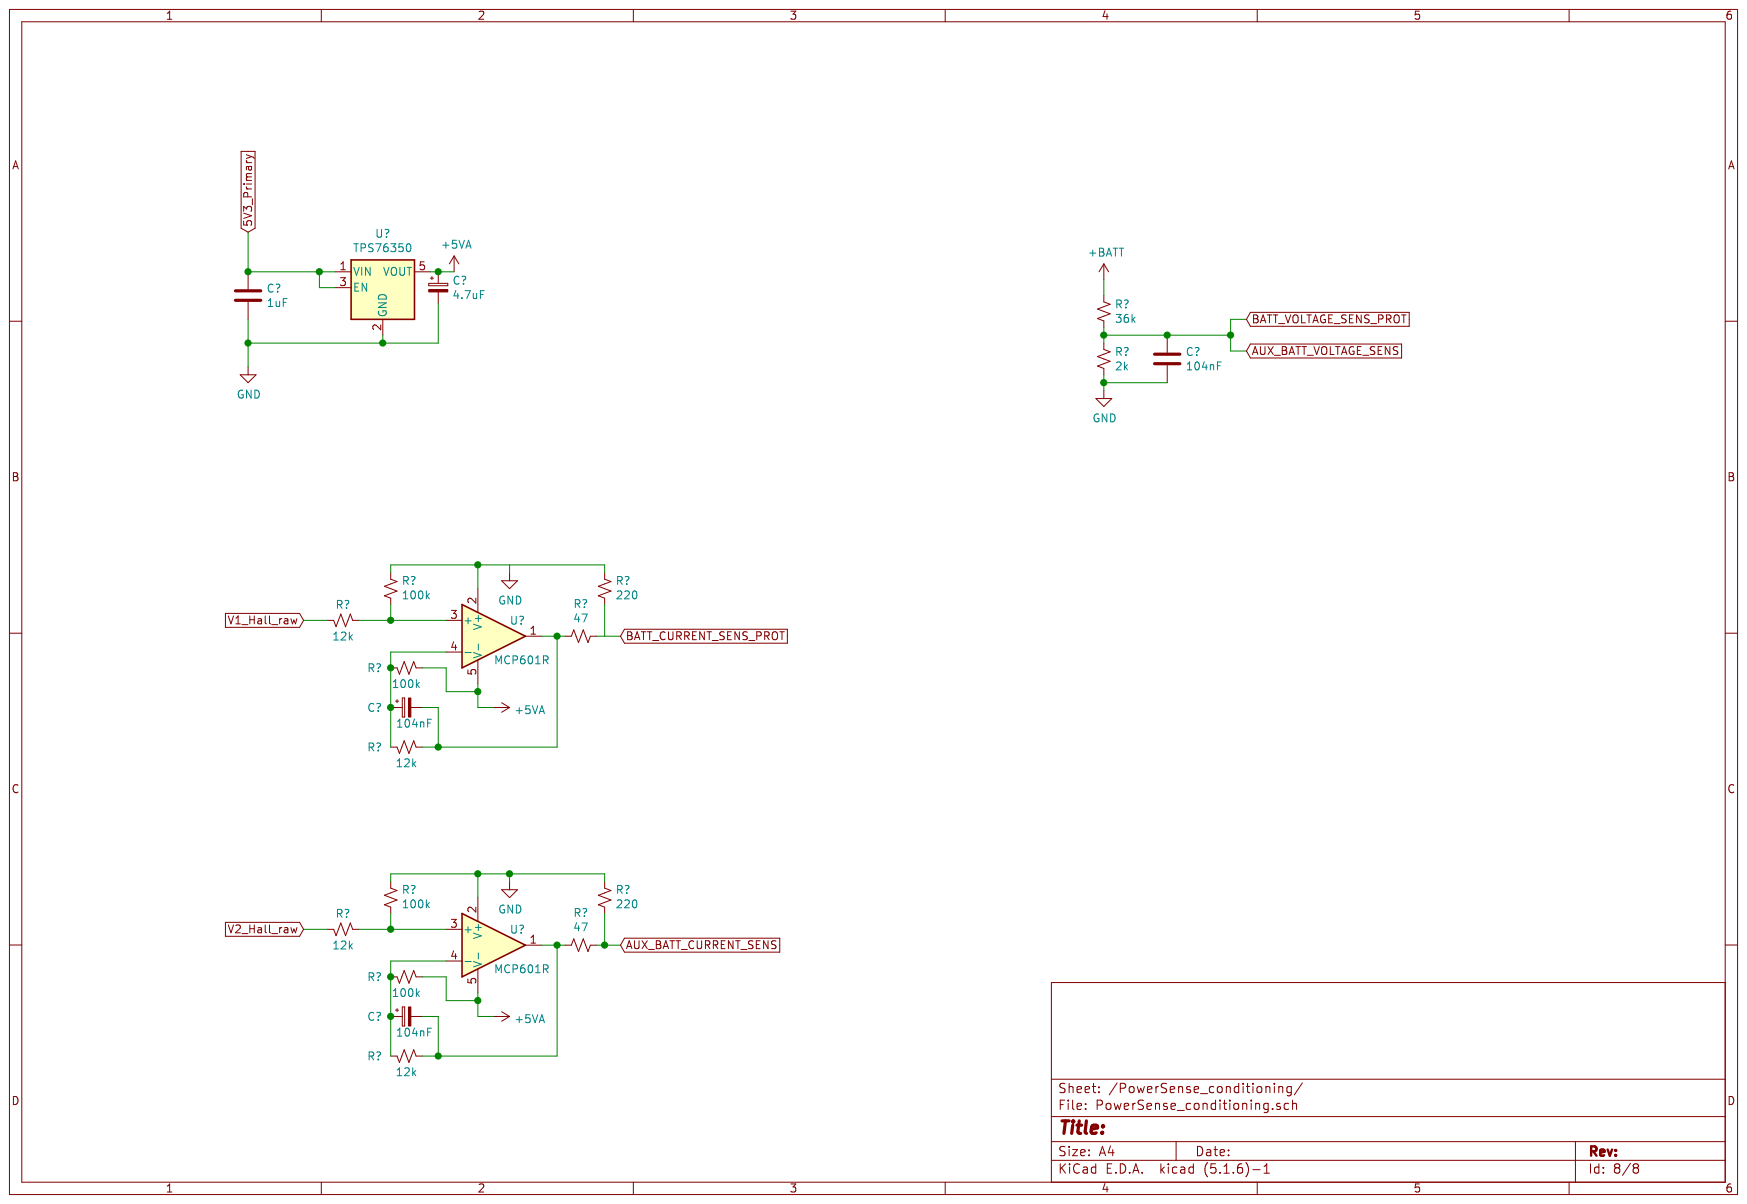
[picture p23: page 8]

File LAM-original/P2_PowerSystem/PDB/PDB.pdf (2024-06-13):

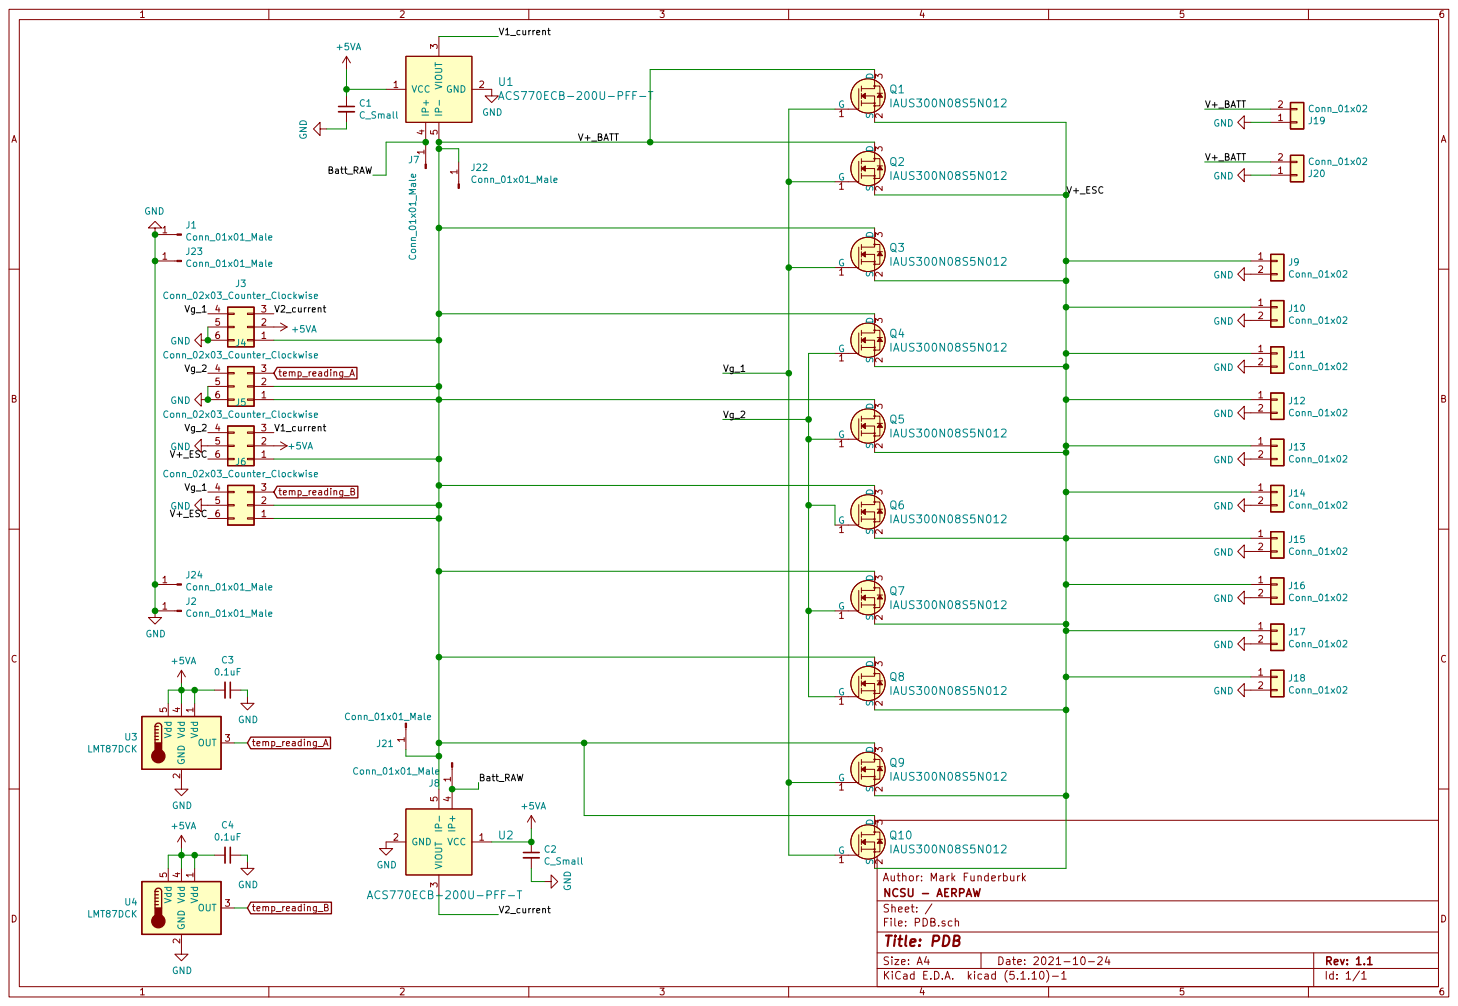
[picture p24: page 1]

File: PDB.sch Sheet: / NCSU - AERPAW

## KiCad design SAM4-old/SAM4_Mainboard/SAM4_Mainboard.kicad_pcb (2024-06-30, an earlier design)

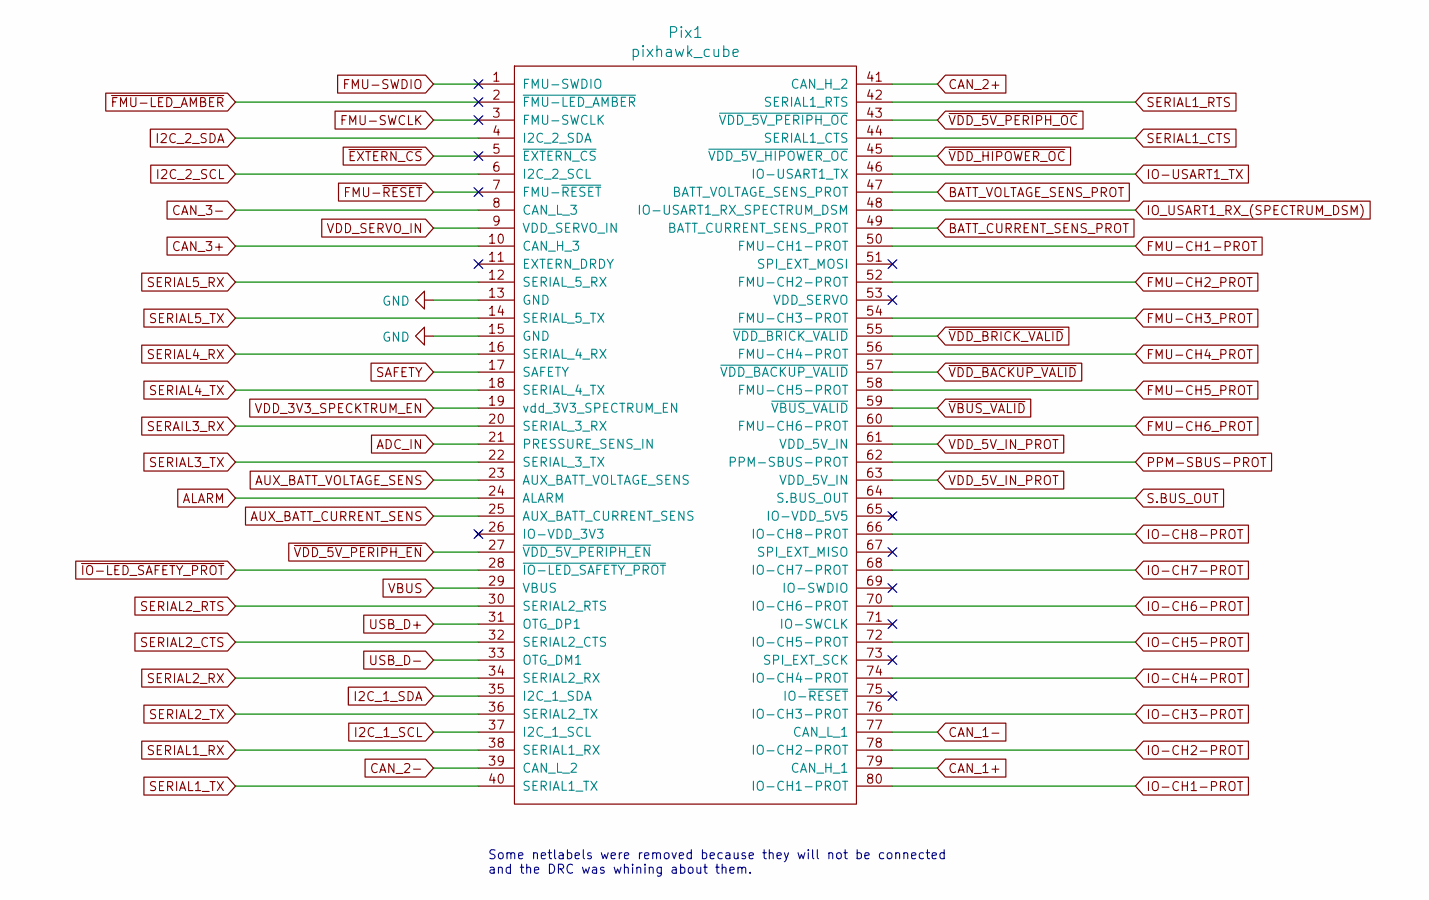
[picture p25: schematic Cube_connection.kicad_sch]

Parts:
Pix1: pixhawk_cube; CUBE_FOOTPRINT

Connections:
ADC_IN: Pix1.21 (PRESSURE_SENS_IN); also elsewhere on the board
ALARM: Pix1.24 (ALARM); also elsewhere on the board
AUX_BATT_CURRENT_SENS: Pix1.25 (AUX_BATT_CURRENT_SENS); also elsewhere on the board
AUX_BATT_VOLTAGE_SENS: Pix1.23 (AUX_BATT_VOLTAGE_SENS)
BATT_CURRENT_SENS_PROT: Pix1.49 (BATT_CURRENT_SENS_PROT); also elsewhere on the board
BATT_VOLTAGE_SENS_PROT: Pix1.47 (BATT_VOLTAGE_SENS_PROT); also elsewhere on the board
CAN_1+: Pix1.79 (CAN_H_1); also elsewhere on the board
CAN_2+: Pix1.41 (CAN_H_2); also elsewhere on the board
CAN_3+: Pix1.10 (CAN_H_3); also elsewhere on the board
FMU-CH1-PROT: Pix1.50 (FMU-CH1-PROT); also elsewhere on the board
FMU-CH2_PROT: Pix1.52 (FMU-CH2-PROT); also elsewhere on the board
FMU-CH3_PROT: Pix1.54 (FMU-CH3-PROT); also elsewhere on the board
FMU-CH4_PROT: Pix1.56 (FMU-CH4-PROT); also elsewhere on the board
FMU-CH5_PROT: Pix1.58 (FMU-CH5-PROT); also elsewhere on the board
FMU-CH6_PROT: Pix1.60 (FMU-CH6-PROT); also elsewhere on the board
FMU-SWCLK: Pix1.3 (FMU-SWCLK)
FMU-SWDIO: Pix1.1 (FMU-SWDIO)
FMU-~RESET: Pix1.7 (FMU-~RESET)
I2C_1_SCL: Pix1.37 (I2C_1_SCL)
I2C_1_SDA: Pix1.35 (I2C_1_SDA)
I2C_2_SCL: Pix1.6 (I2C_2_SCL); also elsewhere on the board
IO-CH1-PROT: Pix1.80 (IO-CH1-PROT); also elsewhere on the board
IO-CH2-PROT: Pix1.78 (IO-CH2-PROT); also elsewhere on the board
IO-CH3-PROT: Pix1.76 (IO-CH3-PROT); also elsewhere on the board
IO-CH4-PROT: Pix1.74 (IO-CH4-PROT); also elsewhere on the board
IO-CH5-PROT: Pix1.72 (IO-CH5-PROT); also elsewhere on the board
IO-CH6-PROT: Pix1.70 (IO-CH6-PROT); also elsewhere on the board
IO-CH7-PROT: Pix1.68 (IO-CH7-PROT); also elsewhere on the board
IO-CH8-PROT: Pix1.66 (IO-CH8-PROT); also elsewhere on the board
IO-USART1_TX: Pix1.46 (IO-USART1_TX)
IO_USART1_RX_(SPECTRUM_DSM): Pix1.48 (IO-USART1_RX_SPECTRUM_DSM)
PPM-SBUS-PROT: Pix1.62 (PPM-SBUS-PROT); also elsewhere on the board
S.BUS_OUT: Pix1.64 (S.BUS_OUT); also elsewhere on the board
SAFETY: Pix1.17 (SAFETY)
SERAIL3_RX: Pix1.20 (SERIAL_3_RX)
SERIAL1_CTS: Pix1.44 (SERIAL1_CTS); also elsewhere on the board
SERIAL1_RTS: Pix1.42 (SERIAL1_RTS); also elsewhere on the board
SERIAL1_TX: Pix1.40 (SERIAL1_TX); also elsewhere on the board
SERIAL2_CTS: Pix1.32 (SERIAL2_CTS); also elsewhere on the board
SERIAL2_RTS: Pix1.30 (SERIAL2_RTS); also elsewhere on the board
SERIAL2_TX: Pix1.36 (SERIAL2_TX); also elsewhere on the board
SERIAL3_TX: Pix1.22 (SERIAL_3_TX)
SERIAL4_RX: Pix1.16 (SERIAL_4_RX)
SERIAL4_TX: Pix1.18 (SERIAL_4_TX)
SERIAL5_RX: Pix1.12 (SERIAL_5_RX); also elsewhere on the board
SERIAL5_TX: Pix1.14 (SERIAL_5_TX)
USB_D+: Pix1.31 (OTG_DP1); also elsewhere on the board
USB_D-: Pix1.33 (OTG_DM1); also elsewhere on the board
VBUS: Pix1.29 (VBUS); also elsewhere on the board
VDD_3V3_SPECKTRUM_EN: Pix1.19 (vdd_3V3_SPECTRUM_EN); also elsewhere on the board
VDD_5V_IN_PROT: Pix1.61 (VDD_5V_IN), Pix1.63 (VDD_5V_IN); also elsewhere on the board
VDD_SERVO_IN: Pix1.9 (VDD_SERVO_IN); also elsewhere on the board
~EXTERN_CS: Pix1.5 (~EXTERN_CS)
~FMU-LED_AMBER: Pix1.2 (~FMU-LED_AMBER)
~IO-LED_SAFETY_PROT: Pix1.28 (~IO-LED_SAFETY_PROT)
~VBUS_VALID: Pix1.59 (~VBUS_VALID); also elsewhere on the board
~VDD_5V_PERIPH_EN: Pix1.27 (~VDD_5V_PERIPH_EN); also elsewhere on the board
~VDD_5V_PERIPH_OC: Pix1.43 (~VDD_5V_PERIPH_OC); also elsewhere on the board
~VDD_BACKUP_VALID: Pix1.57 (~VDD_BACKUP_VALID); also elsewhere on the board
~VDD_BRICK_VALID: Pix1.55 (~VDD_BRICK_VALID); also elsewhere on the board
~VDD_HIPOWER_OC: Pix1.45 (~VDD_5V_HIPOWER_OC); also elsewhere on the board

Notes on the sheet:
Some netlabels were removed because they will not be connected and the DRC was whining about them.

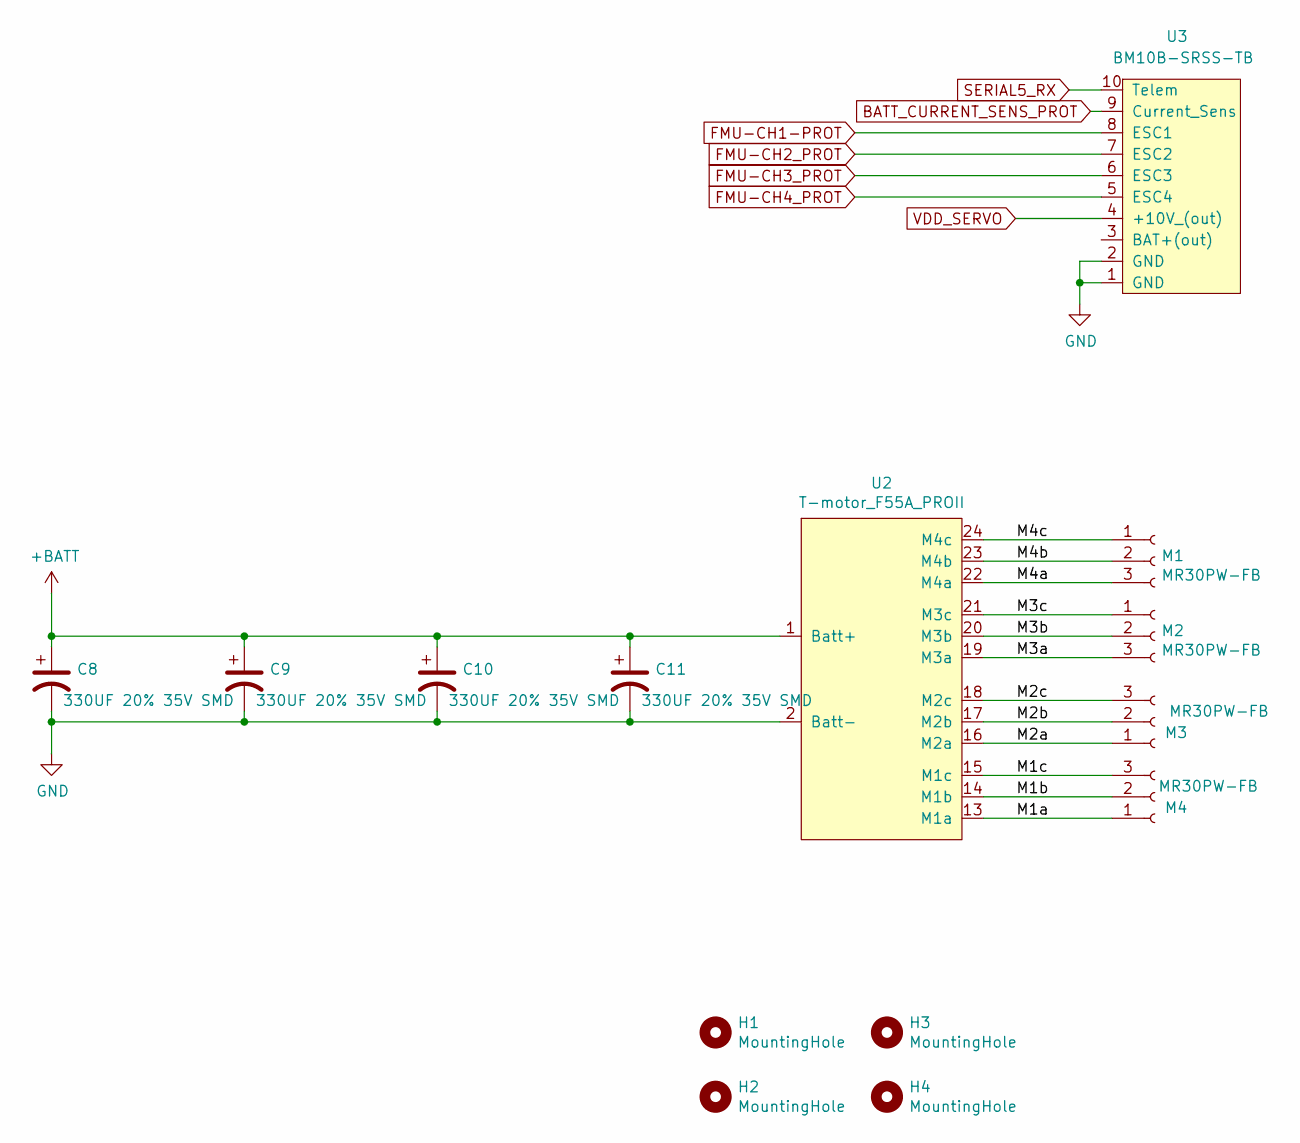
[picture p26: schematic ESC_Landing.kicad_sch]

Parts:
C8, C9, C10, C11: 330UF 20% 35V SMD; CP_Elec_10x10
H1, H2, H3, H4: MountingHole; MountingHole_3.2mm_M3_DIN965_Pad
M1, M2, M3, M4: MR30PW-FB; AMASS_MR30PW-FB_1x03_P3.50mm_Horizontal
U2: T-motor_F55A_PROII; T-motor_55A_ESC
U3: BM10B-SRSS-TB; JST_SH_BM10B-SRSS-TB_1x10-1MP_P1.00mm_Vertical

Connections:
/ESC_Landing/M1a: M4.1, U2.13 (M1a)
/ESC_Landing/M1b: M4.2, U2.14 (M1b)
/ESC_Landing/M1c: M4.3, U2.15 (M1c)
/ESC_Landing/M2a: M3.1, U2.16 (M2a)
/ESC_Landing/M2b: M3.2, U2.17 (M2b)
/ESC_Landing/M2c: M3.3, U2.18 (M2c)
/ESC_Landing/M3a: M2.3, U2.19 (M3a)
/ESC_Landing/M3b: M2.2, U2.20 (M3b)
/ESC_Landing/M3c: M2.1, U2.21 (M3c)
/ESC_Landing/M4a: M1.3, U2.22 (M4a)
/ESC_Landing/M4b: M1.2, U2.23 (M4b)
/ESC_Landing/M4c: M1.1, U2.24 (M4c)
BATT_CURRENT_SENS_PROT: U3.9 (Current_Sens); also elsewhere on the board
FMU-CH1-PROT: U3.8 (ESC1); also elsewhere on the board
FMU-CH2_PROT: U3.7 (ESC2); also elsewhere on the board
FMU-CH3_PROT: U3.6 (ESC3); also elsewhere on the board
FMU-CH4_PROT: U3.5 (ESC4); also elsewhere on the board
SERIAL5_RX: U3.10 (Telem); also elsewhere on the board
VDD_SERVO: U3.4 (+10V_(out)); also elsewhere on the board

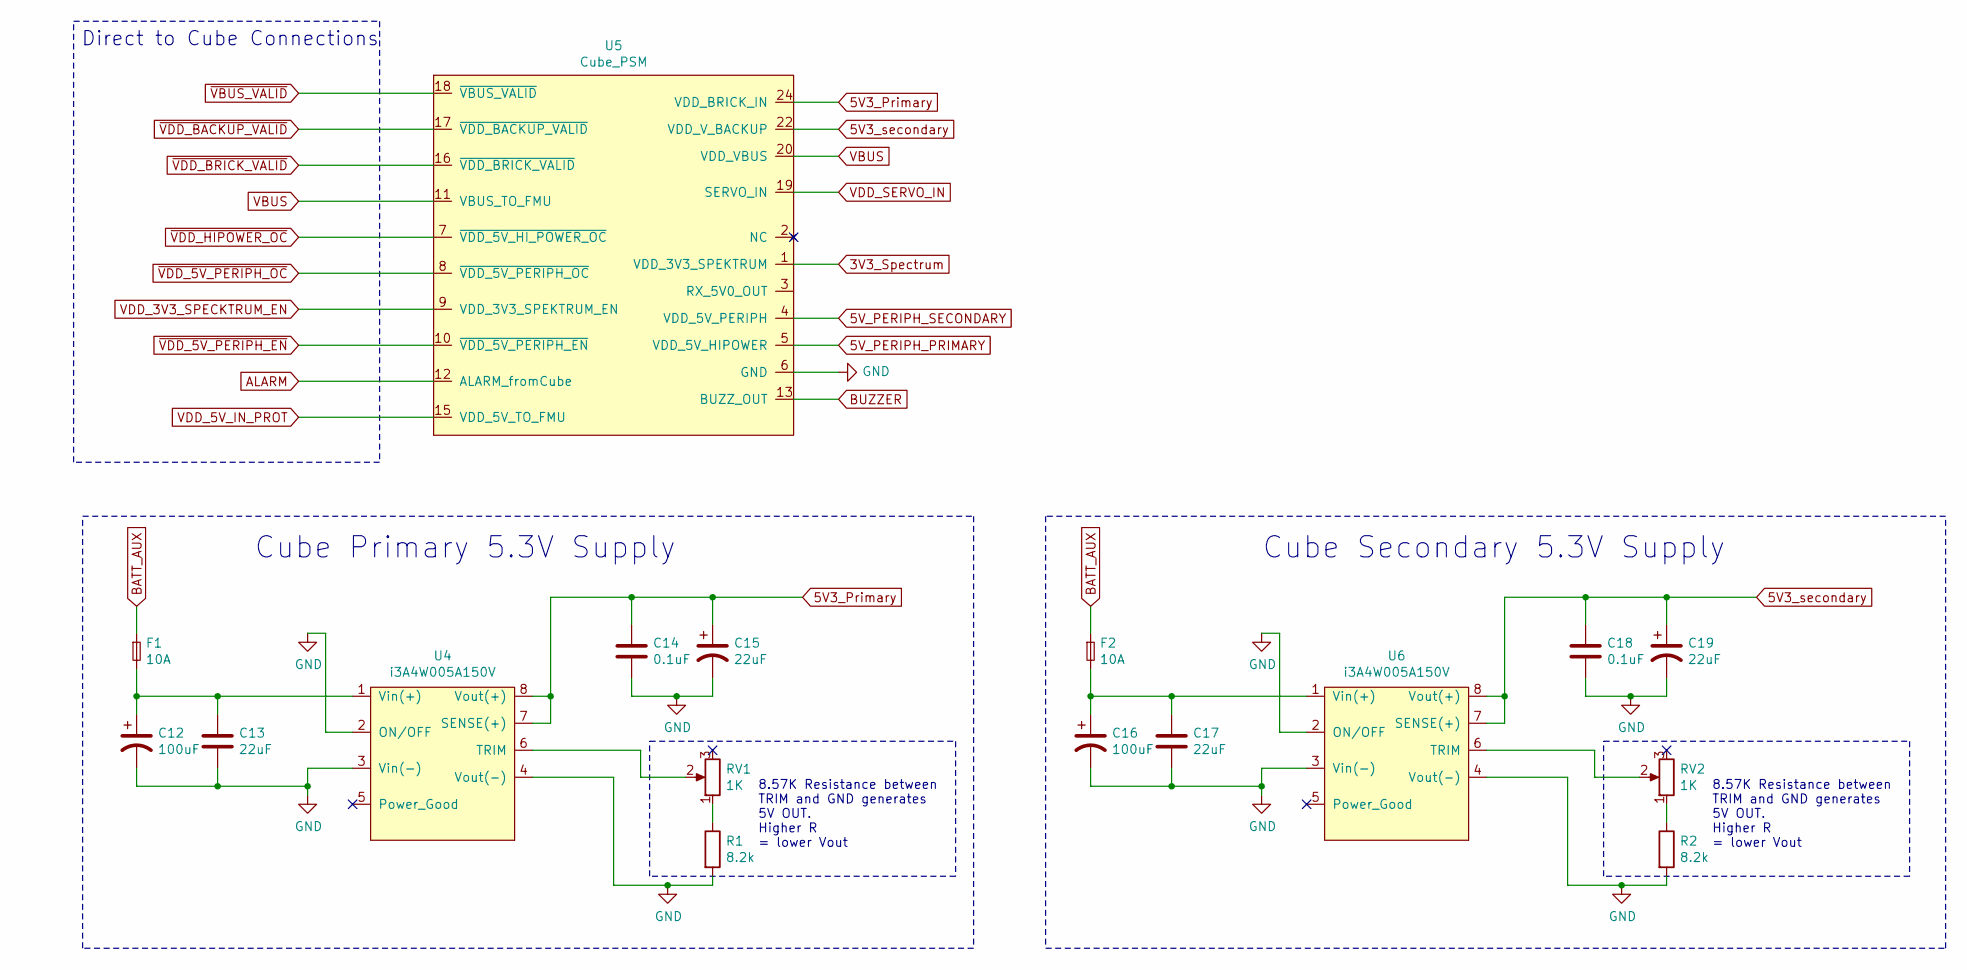
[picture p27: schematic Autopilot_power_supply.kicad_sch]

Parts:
C12, C16: 100uF; CP_Elec_10x10.5
C13, C15, C17, C19: 22uF; C_1206_3216Metric
C14, C18: 0.1uF; C_1206_3216Metric
F1, F2: 10A; Fuse_2512_6332Metric_Pad1.52x3.35mm_HandSolder
R1, R2: 8.2k; R_1206_3216Metric
RV1, RV2: 1K; Potentiometer_Bourns_3266W_Vertical
U4, U6: i3A4W005A150V; 1_32nd_Brick_8pin
U5: Cube_PSM; CUBE_PSM

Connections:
3V3_Spectrum: U5.1 (VDD_3V3_SPEKTRUM)
5V3_Primary: C14.1, C15.1, U4.7 (SENSE(+)), U4.8 (Vout(+)), U5.24 (VDD_BRICK_IN); also elsewhere on the board
5V3_secondary: C18.1, C19.1, U5.22 (VDD_V_BACKUP), U6.7 (SENSE(+)), U6.8 (Vout(+)); also elsewhere on the board
5V_PERIPH_PRIMARY: U5.5 (VDD_5V_HIPOWER); also elsewhere on the board
5V_PERIPH_SECONDARY: U5.4 (VDD_5V_PERIPH); also elsewhere on the board
ALARM: U5.12 (ALARM_fromCube); also elsewhere on the board
BATT_AUX: F1.1, F2.1; also elsewhere on the board
BUZZER: U5.13 (BUZZ_OUT); also elsewhere on the board
unnamed: C12.1, C13.1, F1.2, U4.1 (Vin(+))
unnamed: C16.1, C17.1, F2.2, U6.1 (Vin(+))
unnamed: R1.1, RV1.1
unnamed: R2.1, RV2.1
unnamed: RV1.2, U4.6 (TRIM)
unnamed: RV2.2, U6.6 (TRIM)
VBUS: U5.11 (VBUS_TO_FMU), U5.20 (VDD_VBUS); also elsewhere on the board
VDD_3V3_SPECKTRUM_EN: U5.9 (VDD_3V3_SPEKTRUM_EN); also elsewhere on the board
VDD_5V_IN_PROT: U5.15 (VDD_5V_TO_FMU); also elsewhere on the board
VDD_SERVO_IN: U5.19 (SERVO_IN); also elsewhere on the board
~VBUS_VALID: U5.18 (~VBUS_VALID); also elsewhere on the board
~VDD_5V_PERIPH_EN: U5.10 (~VDD_5V_PERIPH_EN); also elsewhere on the board
~VDD_5V_PERIPH_OC: U5.8 (~VDD_5V_PERIPH_OC); also elsewhere on the board
~VDD_BACKUP_VALID: U5.17 (~VDD_BACKUP_VALID); also elsewhere on the board
~VDD_BRICK_VALID: U5.16 (~VDD_BRICK_VALID); also elsewhere on the board
~VDD_HIPOWER_OC: U5.7 (~VDD_5V_HI_POWER_OC); also elsewhere on the board

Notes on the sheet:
Cube Secondary 5.3V Supply
Cube Primary 5.3V Supply
8.57K Resistance between TRIM and GND generates 5V OUT. Higher R = lower Vout
Direct to Cube Connections

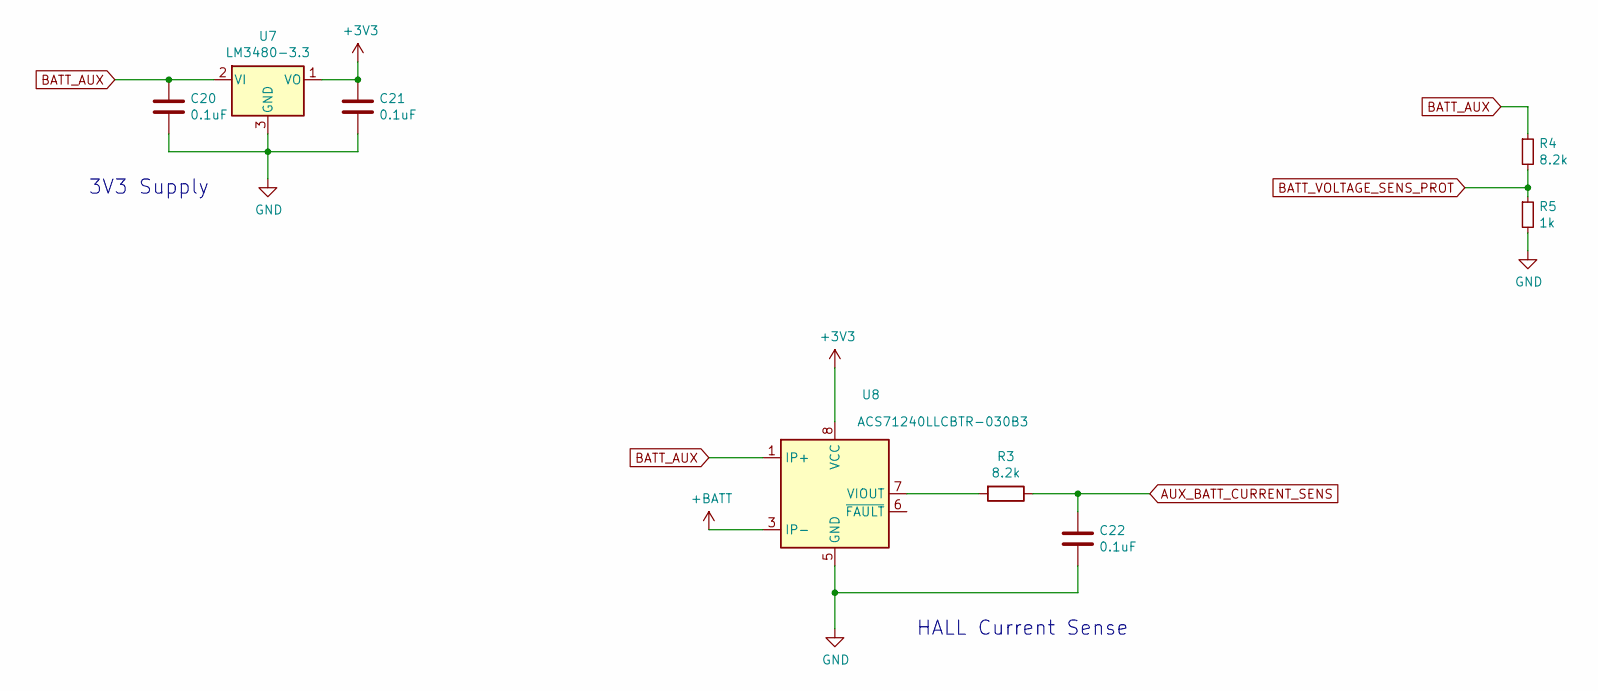
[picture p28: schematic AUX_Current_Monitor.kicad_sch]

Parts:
C20, C21, C22: 0.1uF; C_1206_3216Metric_Pad1.33x1.80mm_HandSolder
R3, R4: 8.2k; R_1206_3216Metric_Pad1.30x1.75mm_HandSolder
R5: 1k; R_1206_3216Metric_Pad1.30x1.75mm_HandSolder
U7: LM3480-3.3; SOT-23
U8: ACS71240LLCBTR-030B3; SOIC-8_3.9x4.9mm_P1.27mm

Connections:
AUX_BATT_CURRENT_SENS: C22.1, R3.1; also elsewhere on the board
BATT_AUX: C20.1, R4.1, U7.2 (VI), U8.1 (IP+), U8.2 (IP+); also elsewhere on the board
BATT_VOLTAGE_SENS_PROT: R4.2, R5.1; also elsewhere on the board
unnamed: R3.2, U8.7 (VIOUT)

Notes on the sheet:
3V3 Supply
HALL Current Sense

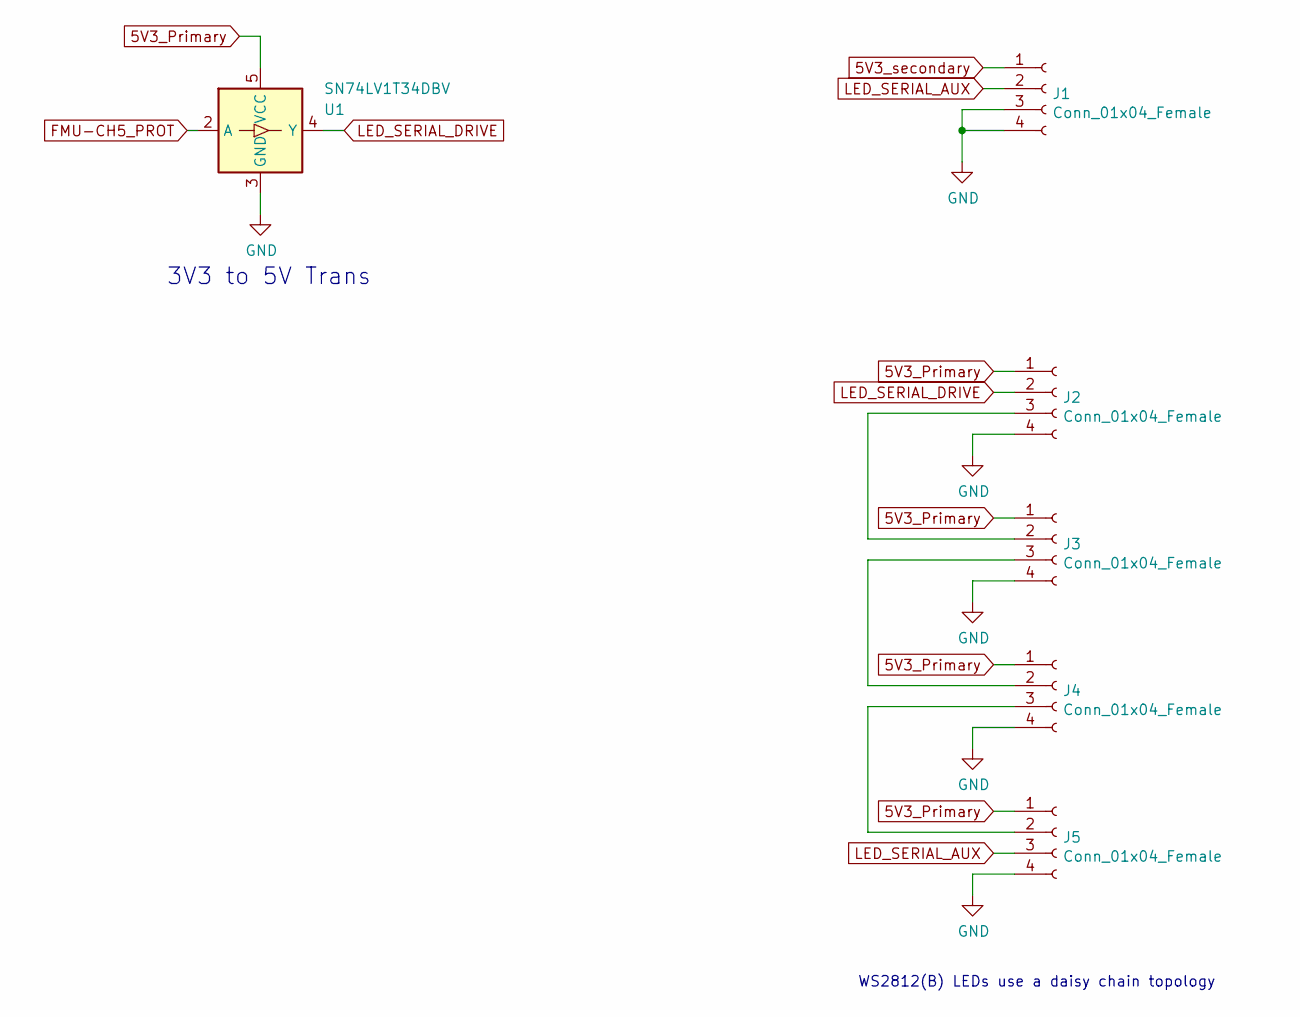
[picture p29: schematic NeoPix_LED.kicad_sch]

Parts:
J1, J2, J3, J4, J5: Conn_01x04_Female; JST_GH_BM04B-GHS-TBT_1x04-1MP_P1.25mm_Vertical
U1: SN74LV1T34DBV; SOT-23-5

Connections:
5V3_Primary: J2.1, J3.1, J4.1, J5.1, U1.5 (VCC); also elsewhere on the board
5V3_secondary: J1.1; also elsewhere on the board
FMU-CH5_PROT: U1.2 (A); also elsewhere on the board
LED_SERIAL_AUX: J1.2, J5.3
LED_SERIAL_DRIVE: J2.2, U1.4 (Y)
unnamed: J2.3, J3.2
unnamed: J3.3, J4.2
unnamed: J4.3, J5.2

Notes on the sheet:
WS2812(B) LEDs use a daisy chain topology
3V3 to 5V Trans

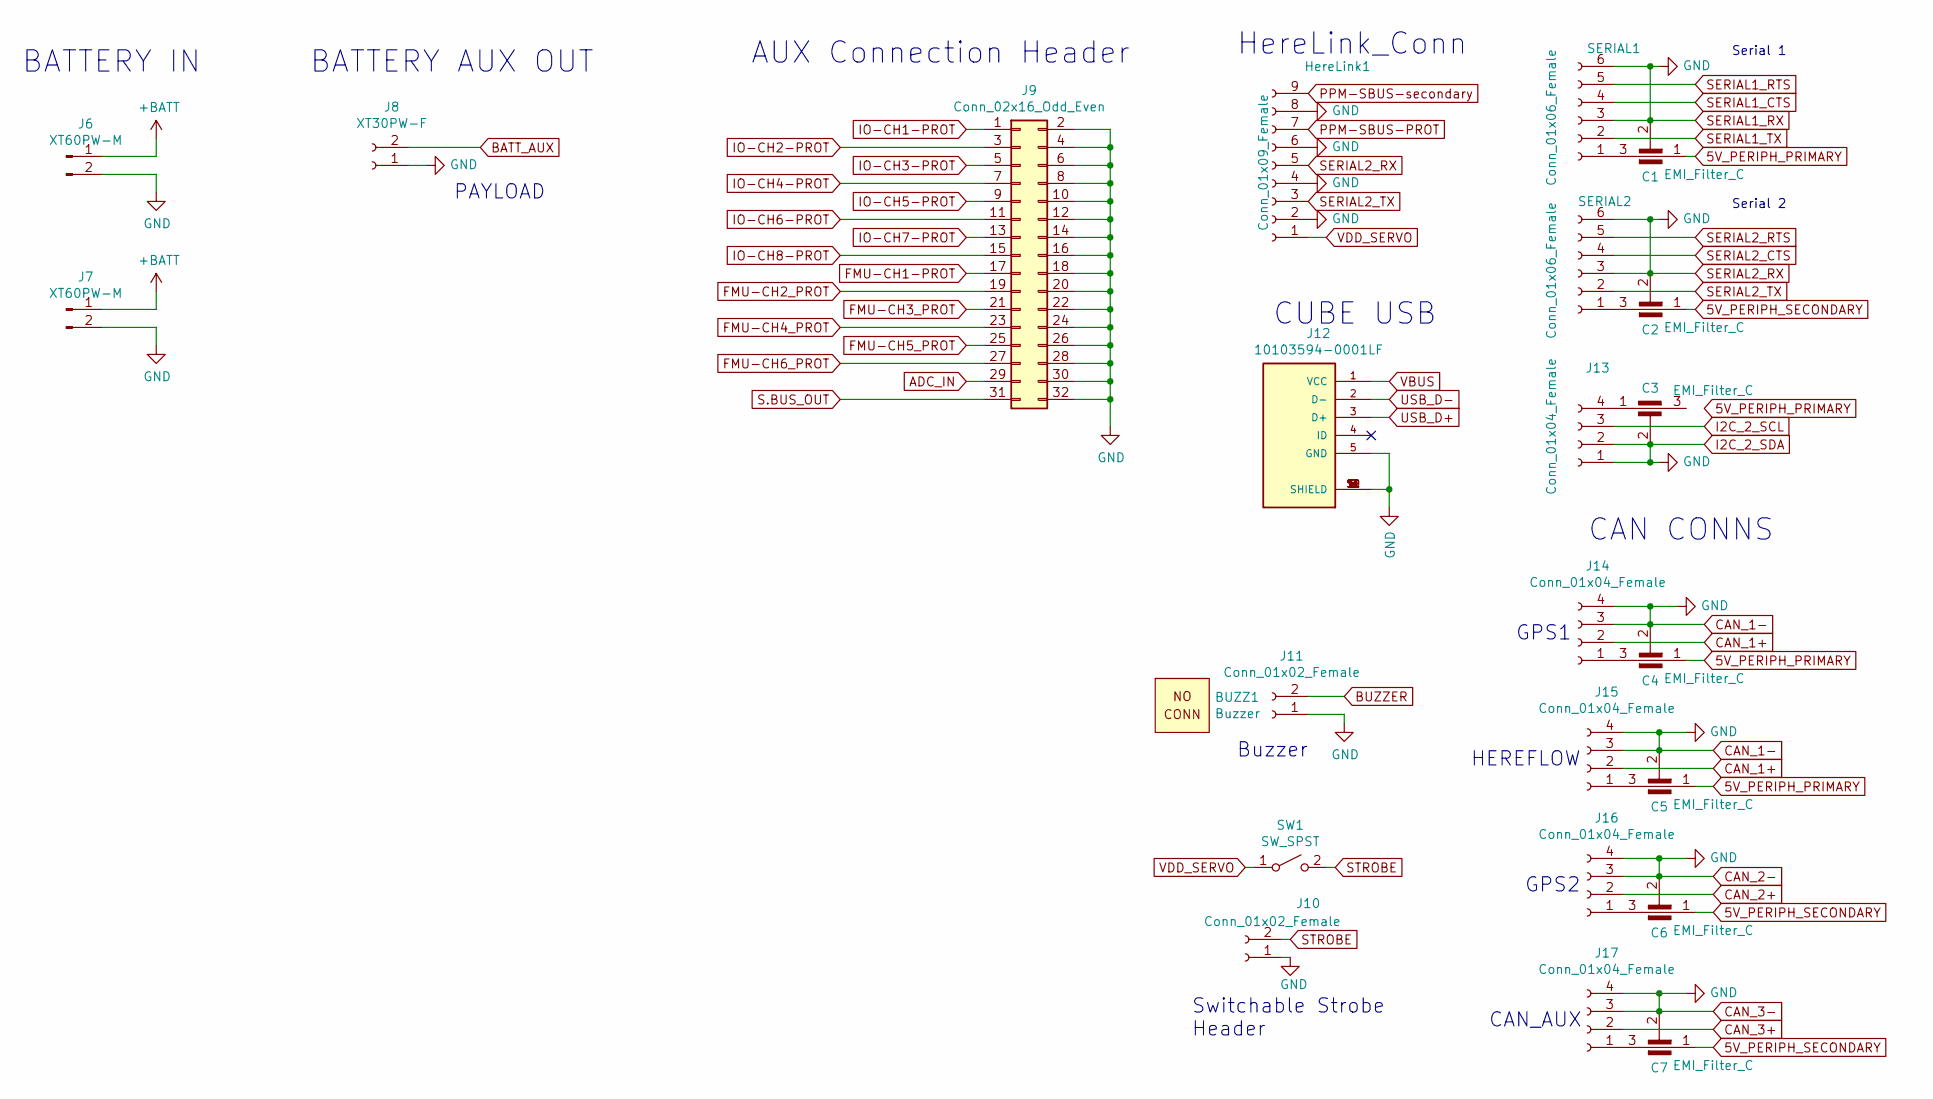
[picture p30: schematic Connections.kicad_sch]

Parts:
BUZZ1: Buzzer; BUZZER
C1, C2, C3, C4, C5, C6, C7: EMI_Filter_C; FIL_NFM21HC224R1A3D
HereLink1: Conn_01x09_Female; JST_GH_SM09B-GHS-TB_1x09-1MP_P1.25mm_Horizontal
J6, J7: XT60PW-M; AMASS_XT60PW-M
J8: XT30PW-F; AMASS_XT30PW-F_1x02_P2.50mm_Horizontal
J9: Conn_02x16_Odd_Even; PinHeader_2x16_P2.54mm_Vertical
J10: Conn_01x02_Female; Molex_CLIK-Mate_502386-0270_1x02-1MP_P1.25mm_Horizontal
J11: Conn_01x02_Female; BUZZ_CONN
J12: 10103594-0001LF; AMPHENOL_10103594-0001LF
J13, J14, J15, J16, J17: Conn_01x04_Female; JST_GH_BM04B-GHS-TBT_1x04-1MP_P1.25mm_Vertical
SERIAL1, SERIAL2: Conn_01x06_Female; JST_GH_BM06B-GHS-TBT_1x06-1MP_P1.25mm_Vertical
SW1: SW_SPST; Slide-Switch_5x5

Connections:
5V_PERIPH_PRIMARY: C1.1, C4.1, C5.1; also elsewhere on the board
5V_PERIPH_SECONDARY: C2.1, C6.1, C7.1; also elsewhere on the board
ADC_IN: J9.29; also elsewhere on the board
BATT_AUX: J8.2; also elsewhere on the board
BUZZER: J11.2; also elsewhere on the board
CAN_1+: J14.2, J15.2; also elsewhere on the board
CAN_2+: J16.2; also elsewhere on the board
CAN_3+: J17.2; also elsewhere on the board
FMU-CH1-PROT: J9.17; also elsewhere on the board
FMU-CH2_PROT: J9.19; also elsewhere on the board
FMU-CH3_PROT: J9.21; also elsewhere on the board
FMU-CH4_PROT: J9.23; also elsewhere on the board
FMU-CH5_PROT: J9.25; also elsewhere on the board
FMU-CH6_PROT: J9.27; also elsewhere on the board
I2C_2_SCL: J13.3; also elsewhere on the board
IO-CH1-PROT: J9.1; also elsewhere on the board
IO-CH2-PROT: J9.3; also elsewhere on the board
IO-CH3-PROT: J9.5; also elsewhere on the board
IO-CH4-PROT: J9.7; also elsewhere on the board
IO-CH5-PROT: J9.9; also elsewhere on the board
IO-CH6-PROT: J9.11; also elsewhere on the board
IO-CH7-PROT: J9.13; also elsewhere on the board
IO-CH8-PROT: J9.15; also elsewhere on the board
unnamed: C1.3, SERIAL1.1
unnamed: C2.3, SERIAL2.1
unnamed: C3.1, J13.4
unnamed: C4.3, J14.1
unnamed: C5.3, J15.1
unnamed: C6.3, J16.1
unnamed: C7.3, J17.1
PPM-SBUS-PROT: HereLink1.7; also elsewhere on the board
PPM-SBUS-secondary: HereLink1.9
S.BUS_OUT: J9.31; also elsewhere on the board
SERIAL1_CTS: SERIAL1.4; also elsewhere on the board
SERIAL1_RTS: SERIAL1.5; also elsewhere on the board
SERIAL1_TX: SERIAL1.2; also elsewhere on the board
SERIAL2_CTS: SERIAL2.4; also elsewhere on the board
SERIAL2_RTS: SERIAL2.5; also elsewhere on the board
SERIAL2_TX: HereLink1.3, SERIAL2.2; also elsewhere on the board
STROBE: J10.2, SW1.2 (B)
USB_D+: J12.3 (D+); also elsewhere on the board
USB_D-: J12.2 (D-); also elsewhere on the board
VBUS: J12.1 (VCC); also elsewhere on the board
VDD_SERVO: HereLink1.1, SW1.1 (A); also elsewhere on the board

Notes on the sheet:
Switchable Strobe Header
CAN_AUX
Serial 2
Buzzer
BATTERY IN
AUX Connection Header
GPS2
Serial 1
CUBE USB
CAN CONNS
HEREFLOW
PAYLOAD
HereLink_Conn
BATTERY AUX OUT
GPS1

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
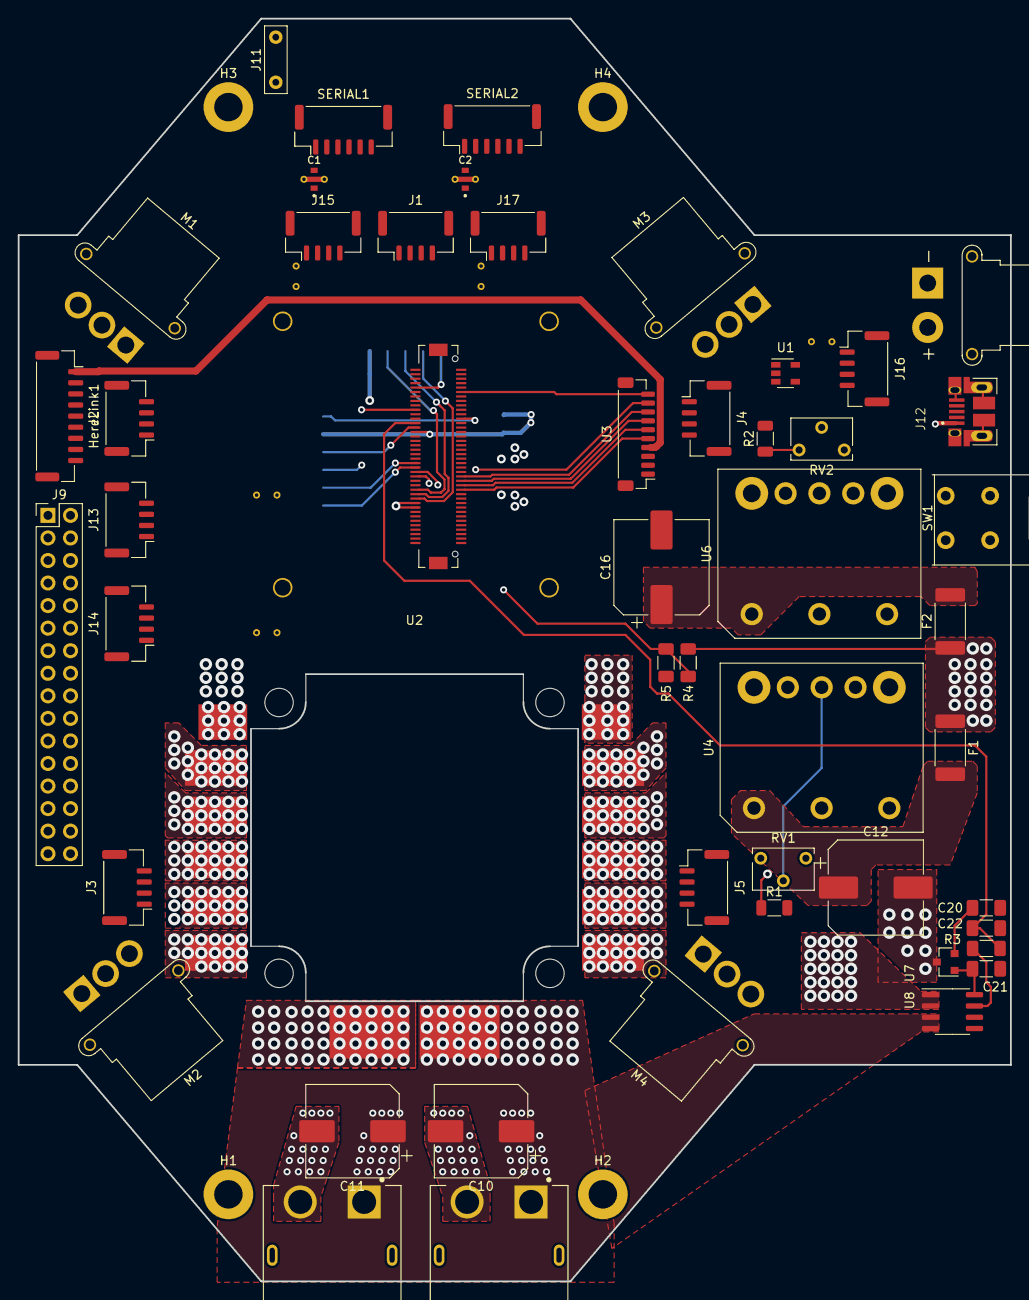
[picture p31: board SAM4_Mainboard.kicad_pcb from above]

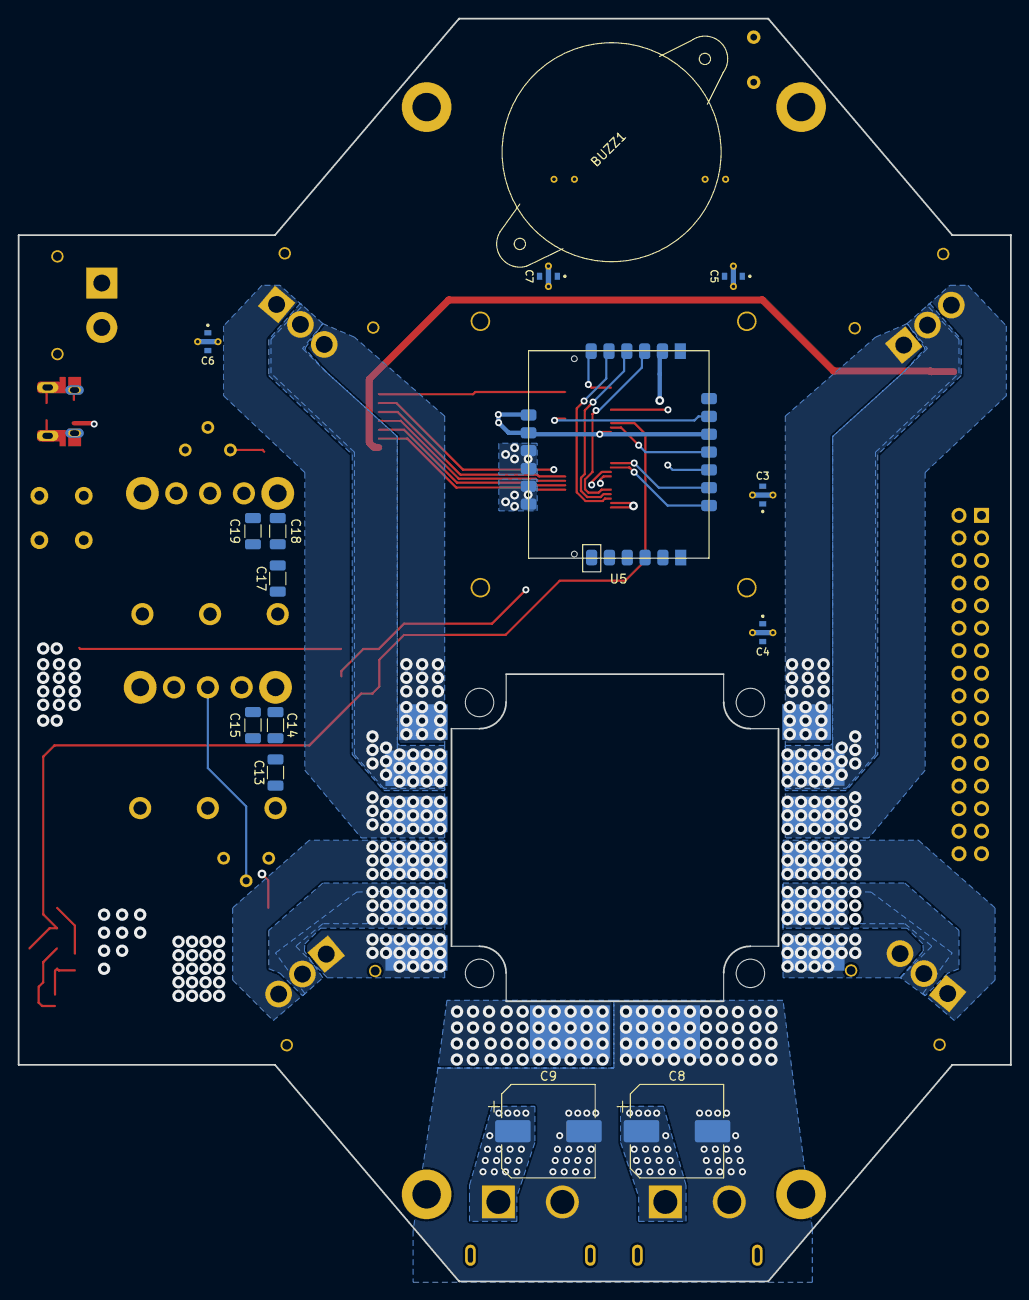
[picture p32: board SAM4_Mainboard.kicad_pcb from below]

Board: 4 copper layers, 111.7 x 142.2 mm, 69 parts (15 on the bottom side), 91 nets.

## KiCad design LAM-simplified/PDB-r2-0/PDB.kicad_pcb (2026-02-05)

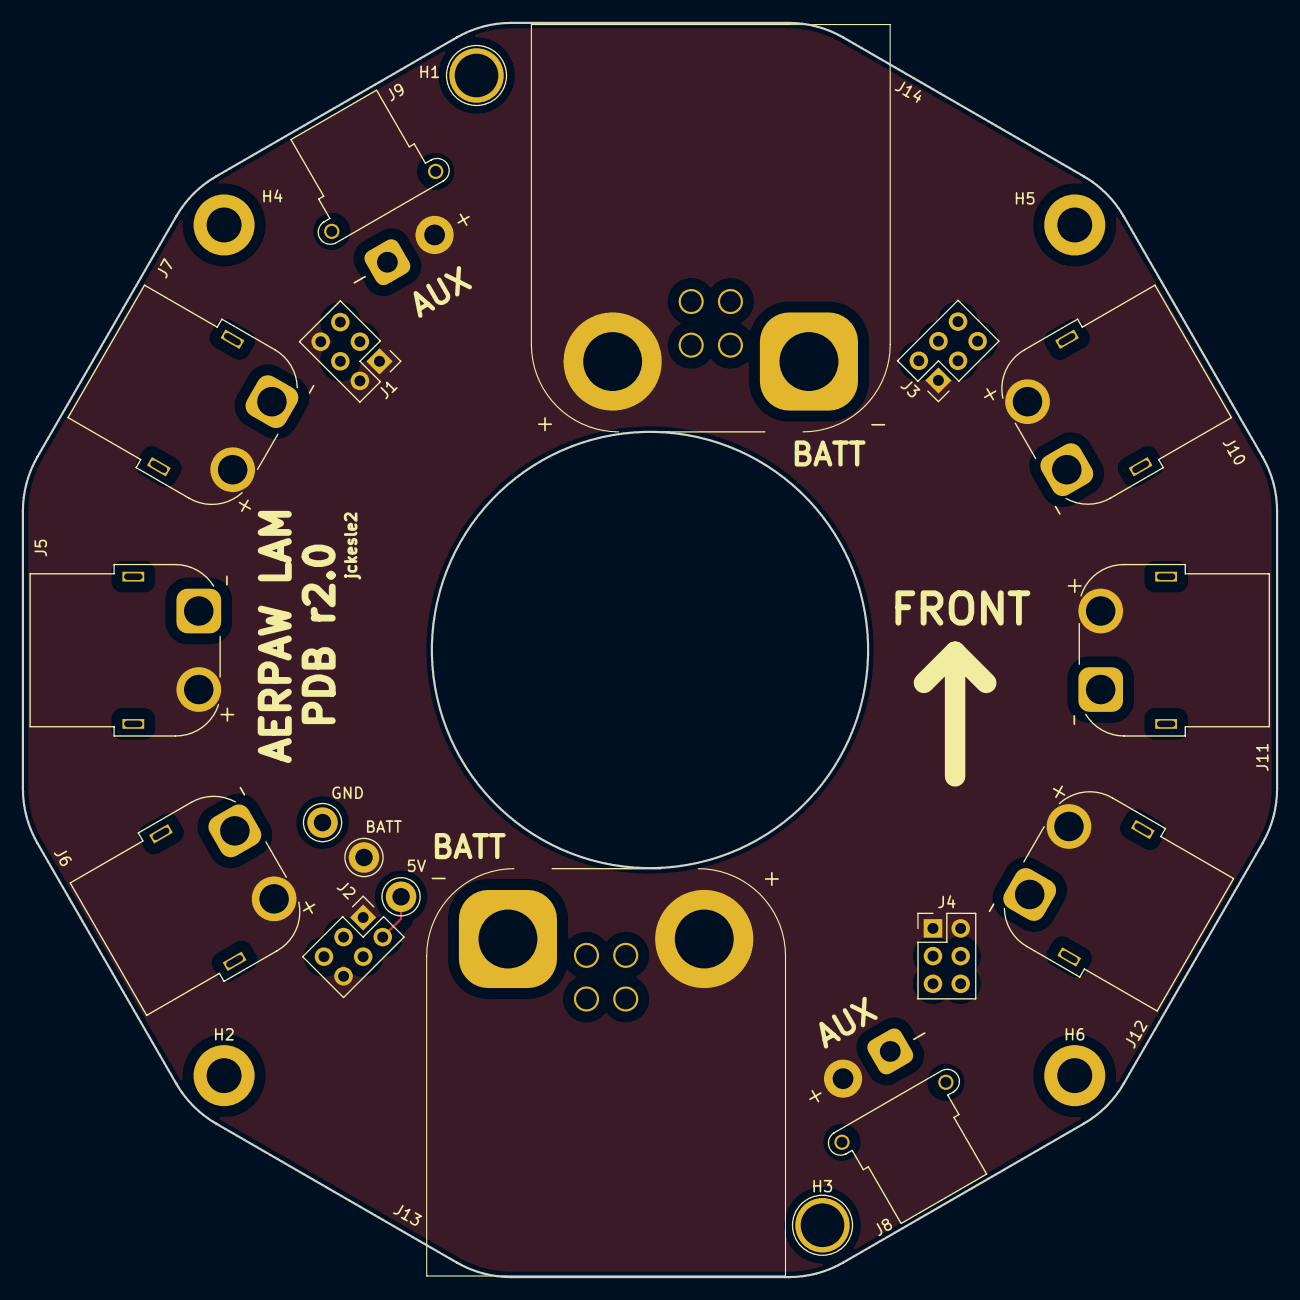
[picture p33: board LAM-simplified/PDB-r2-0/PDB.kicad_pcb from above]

Board: 2 copper layers, 115.0 x 115.0 mm, 23 parts (0 on the bottom side), 3 nets.

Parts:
5V: TestPoint_Flag; TestPoint_Keystone_5010-5014_Multipurpose
BATT: TestPoint_Flag; TestPoint_Keystone_5010-5014_Multipurpose
GND: TestPoint_Flag; TestPoint_Keystone_5010-5014_Multipurpose
H1, H3: M4; TestPoint_Plated_Hole_D4.0mm
H2, H4, H5, H6: M3; MountingHole_3.2mm_M3_DIN965_Pad
J1, J2, J3, J4: 2.54mm 2x3; PinHeader_2x03_P2.54mm_Vertical
J5, J6, J7, J10, J11, J12: xt60-female; AMASS_XT60PW-F_1x02_P7.20mm_Horizontal
J8, J9: xt30-female; AMASS_XT30PW-F_1x02_P2.50mm_Horizontal
J13, J14: AS150UPW-M(ale); AS150UPW(2+4-)M.G.Y

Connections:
+5V: 5V.1, J2.2, J3.2
/vbat: BATT.1, J1.1, J1.2, J1.6, J2.1, J2.6, J3.1, J4.1, J4.2, J5.2, J6.2, J7.2, J8.2, J9.2, J10.2, J11.2, J12.2, J13.2, J14.2
GND: GND.1, H1.1, H2.1, H3.1, H4.1, H5.1, H6.1, J1.5, J2.5, J3.5, J3.6, J4.5, J4.6, J5.1, J6.1, J7.1, J8.1, J9.1, J10.1, J11.1, J12.1, J13.1, J14.1

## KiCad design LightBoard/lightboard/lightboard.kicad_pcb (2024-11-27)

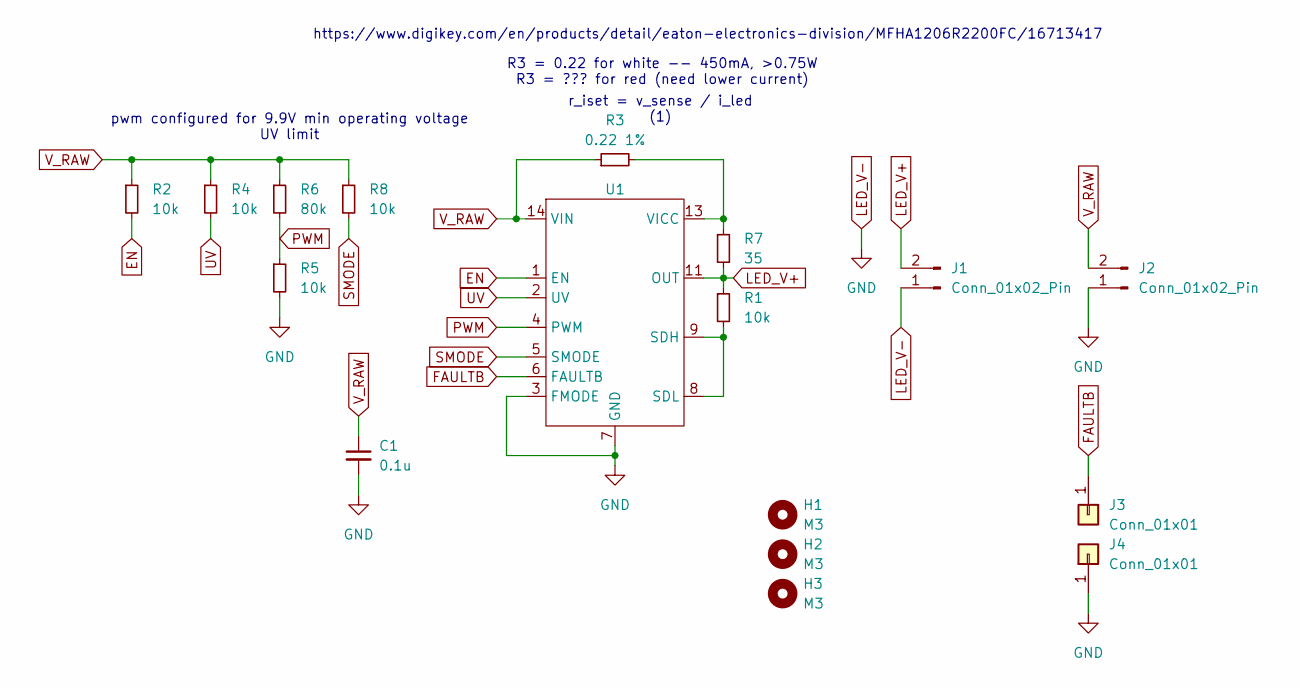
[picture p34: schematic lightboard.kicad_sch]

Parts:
C1: 0.1u; C_1206_3216Metric
H1, H2, H3: M3; MountingHole_3.2mm_M3
J1, J2: Conn_01x02_Pin; JST_EH_S2B-EH_1x02_P2.50mm_Horizontal
J3, J4: Conn_01x01; TestPoint_Pad_1.5x1.5mm
R1, R2, R4, R5, R8: 10k; R_1206_3216Metric
R3: 0.22 1%; R_1206_3216Metric
R6: 80k; R_1206_3216Metric
R7: 35; R_1206_3216Metric
U1: IS32LT3140A

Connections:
EN: R2.2, U1.1 (EN)
FAULTB: J3.1, U1.6 (FAULTB)
LED_V+: J1.2, R1.1, R7.2, U1.11 (OUT)
LED_V-: C1.2, J1.1, J2.1, J4.1, R5.2, U1.3 (FMODE), U1.7 (GND)
unnamed: R1.2, U1.8 (SDL), U1.9 (SDH)
unnamed: R3.2, R7.1, U1.13 (VICC)
PWM: R5.1, R6.2, U1.4 (PWM)
SMODE: R8.2, U1.5 (SMODE)
UV: R4.2, U1.2 (UV)
V_RAW: C1.1, J2.2, R2.1, R3.1, R4.1, R6.1, R8.1, U1.14 (VIN)

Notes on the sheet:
r_iset = v_sense / i_led (1)
https://www.digikey.com/en/products/detail/eaton-electronics-division/MFHA1206R2200FC/16713417
R3 = 0.22 for white -- 450mA, >0.75W R3 = ??? for red (need lower current)
pwm configured for 9.9V min operating voltage UV limit

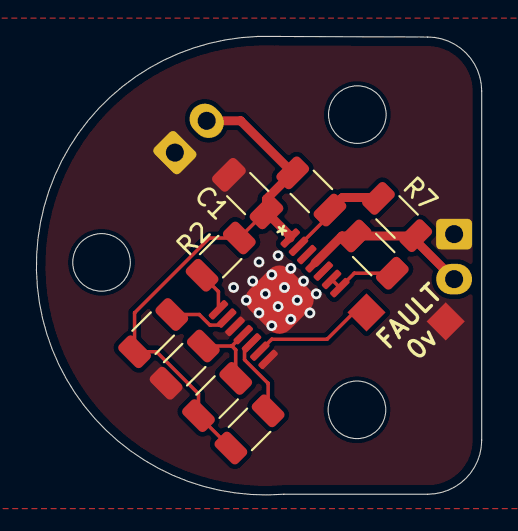
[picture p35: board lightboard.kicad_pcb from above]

Board: 2 copper layers, 24.7 x 25.5 mm, 17 parts (1 on the bottom side), 10 nets.

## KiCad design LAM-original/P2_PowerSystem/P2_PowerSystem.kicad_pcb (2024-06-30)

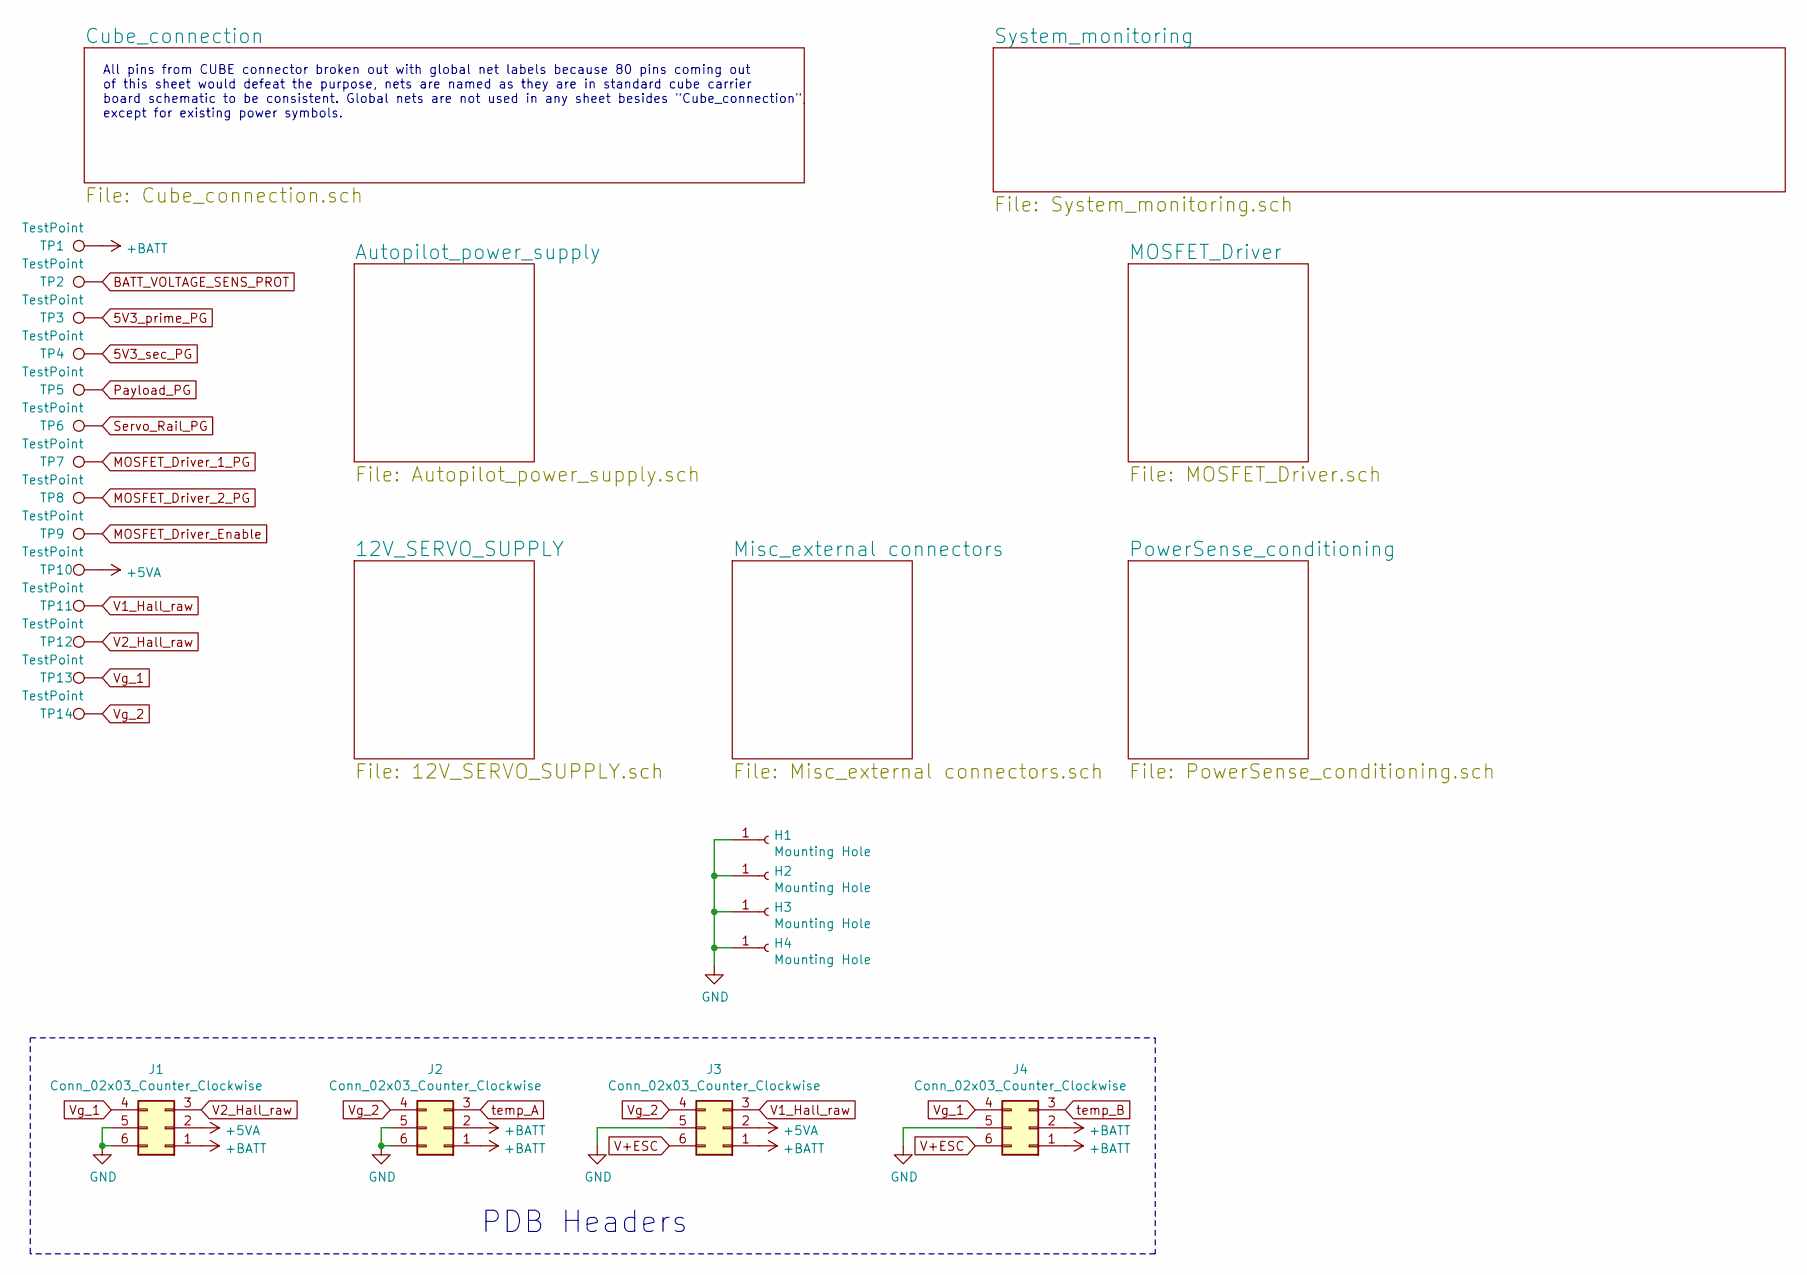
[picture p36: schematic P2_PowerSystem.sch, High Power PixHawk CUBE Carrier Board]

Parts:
H1, H2, H3, H4: Mounting Hole; MountingHole_3.2mm_M3_DIN965_Pad; Meta_Part DNP
J1, J2, J3, J4: Conn_02x03_Counter_Clockwise; SAMTEC_ESQ-103-44-L-D; Meta_Part HEADER-F 0.1\" 2x3 POS 19mm THT
TP1, TP2, TP3, TP4, TP5, TP6, TP7, TP8, TP9, TP10, TP11, TP12, TP13, TP14: TestPoint; TestPoint_Pad_1.5x1.5mm; Meta_Part DNP

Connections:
5V3_prime_PG: TP3.1; also elsewhere on the board
5V3_sec_PG: TP4.1; also elsewhere on the board
+5VA: J1.2, J3.2, TP10.1; also elsewhere on the board
+BATT: J1.1, J2.1, J2.2, J3.1, J4.1, J4.2, TP1.1; also elsewhere on the board
BATT_VOLTAGE_SENS_PROT: TP2.1; also elsewhere on the board
GND: H1.1, H2.1, H3.1, H4.1, J1.5, J1.6, J2.5, J2.6, J3.5, J4.5; also elsewhere on the board
MOSFET_Driver_1_PG: TP7.1; also elsewhere on the board
MOSFET_Driver_2_PG: TP8.1; also elsewhere on the board
MOSFET_Driver_Enable: TP9.1; also elsewhere on the board
Payload_PG: TP5.1; also elsewhere on the board
Servo_Rail_PG: TP6.1; also elsewhere on the board
V1_Hall_raw: J3.3, TP11.1; also elsewhere on the board
V2_Hall_raw: J1.3, TP12.1; also elsewhere on the board
V+ESC: J3.6, J4.6; also elsewhere on the board
Vg_1: J1.4, J4.4, TP13.1; also elsewhere on the board
Vg_2: J2.4, J3.4, TP14.1; also elsewhere on the board
temp_A: J2.3; also elsewhere on the board
temp_B: J4.3; also elsewhere on the board

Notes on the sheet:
PDB Headers
All pins from CUBE connector broken out with global net labels because 80 pins coming out of this sheet would defeat the purpose, nets are named as they are in standard cube carrier board schematic to be consistent. Global nets are not used in any sheet besides "Cube_connection", except for existin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


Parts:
Pix1: pixhawk_cube; DF1710H80DP05V57; Meta_Part DF17 4mm 80POS

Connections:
ADC_IN: Pix1.21 (PRESSURE_SENS_IN); also elsewhere on the board
ALARM: Pix1.24 (ALARM); also elsewhere on the board
AUX_BATT_CURRENT_SENS: Pix1.25 (AUX_BATT_CURRENT_SENS); also elsewhere on the board
AUX_BATT_VOLTAGE_SENS: Pix1.23 (AUX_BATT_VOLTAGE_SENS); also elsewhere on the board
BATT_CURRENT_SENS_PROT: Pix1.49 (BATT_CURRENT_SENS_PROT); also elsewhere on the board
BATT_VOLTAGE_SENS_PROT: Pix1.47 (BATT_VOLTAGE_SENS_PROT); also elsewhere on the board
CAN_1+: Pix1.79 (CAN_H_1); also elsewhere on the board
CAN_1-: Pix1.77 (CAN_L_1); also elsewhere on the board
CAN_2+: Pix1.41 (CAN_H_2); also elsewhere on the board
CAN_2-: Pix1.39 (CAN_L_2); also elsewhere on the board
CAN_3+: Pix1.10 (CAN_H_3); also elsewhere on the board
CAN_3-: Pix1.8 (CAN_L_3); also elsewhere on the board
FMU-CH1-PROT: Pix1.50 (FMU-CH1-PROT); also elsewhere on the board
FMU-CH2_PROT: Pix1.52 (FMU-CH2-PROT); also elsewhere on the board
FMU-CH3_PROT: Pix1.54 (FMU-CH3-PROT); also elsewhere on the board
FMU-CH4_PROT: Pix1.56 (FMU-CH4-PROT); also elsewhere on the board
FMU-CH5_PROT: Pix1.58 (FMU-CH5-PROT); also elsewhere on the board
FMU-CH6_PROT: Pix1.60 (FMU-CH6-PROT); also elsewhere on the board
FMU-SWCLK: Pix1.3 (FMU-SWCLK)
FMU-SWDIO: Pix1.1 (FMU-SWDIO)
FMU-~RESET: Pix1.7 (FMU-~RESET)
GND: Pix1.13 (GND), Pix1.15 (GND); also elsewhere on the board
I2C_1_SCL: Pix1.37 (I2C_1_SCL); also elsewhere on the board
I2C_1_SDA: Pix1.35 (I2C_1_SDA); also elsewhere on the board
I2C_2_SCL: Pix1.6 (I2C_2_SCL); also elsewhere on the board
I2C_2_SDA: Pix1.4 (I2C_2_SDA); also elsewhere on the board
IO-CH1-PROT: Pix1.80 (IO-CH1-PROT); also elsewhere on the board
IO-CH2-PROT: Pix1.78 (IO-CH2-PROT); also elsewhere on the board
IO-CH3-PROT: Pix1.76 (IO-CH3-PROT); also elsewhere on the board
IO-CH4-PROT: Pix1.74 (IO-CH4-PROT); also elsewhere on the board
IO-CH5-PROT: Pix1.72 (IO-CH5-PROT); also elsewhere on the board
IO-CH6-PROT: Pix1.70 (IO-CH6-PROT); also elsewhere on the board
IO-CH7-PROT: Pix1.68 (IO-CH7-PROT); also elsewhere on the board
IO-CH8-PROT: Pix1.66 (IO-CH8-PROT); also elsewhere on the board
IO-USART1_TX: Pix1.46 (IO-USART1_TX)
IO_USART1_RX_(SPECTRUM_DSM): Pix1.48 (IO-USART1_RX_SPECTRUM_DSM)
PPM-SBUS-PROT: Pix1.62 (PPM-SBUS-PROT); also elsewhere on the board
S.BUS_OUT: Pix1.64 (S.BUS_OUT); also elsewhere on the board
SAFETY: Pix1.17 (SAFETY); also elsewhere on the board
SERAIL3_RX: Pix1.20 (SERIAL_3_RX); also elsewhere on the board
SERIAL1_CTS: Pix1.44 (SERIAL1_CTS); also elsewhere on the board
SERIAL1_RTS: Pix1.42 (SERIAL1_RTS); also elsewhere on the board
SERIAL1_RX: Pix1.38 (SERIAL1_RX); also elsewhere on the board
SERIAL1_TX: Pix1.40 (SERIAL1_TX); also elsewhere on the board
SERIAL2_CTS: Pix1.32 (SERIAL2_CTS); also elsewhere on the board
SERIAL2_RTS: Pix1.30 (SERIAL2_RTS); also elsewhere on the board
SERIAL2_RX: Pix1.34 (SERIAL2_RX); also elsewhere on the board
SERIAL2_TX: Pix1.36 (SERIAL2_TX); also elsewhere on the board
SERIAL3_TX: Pix1.22 (SERIAL_3_TX); also elsewhere on the board
SERIAL4_RX: Pix1.16 (SERIAL_4_RX); also elsewhere on the board
SERIAL4_TX: Pix1.18 (SERIAL_4_TX); also elsewhere on the board
SERIAL5_RX: Pix1.12 (SERIAL_5_RX); also elsewhere on the board
SERIAL5_TX: Pix1.14 (SERIAL_5_TX); also elsewhere on the board
USB_D+: Pix1.31 (OTG_DP1); also elsewhere on the board
USB_D-: Pix1.33 (OTG_DM1); also elsewhere on the board
VBUS: Pix1.29 (VBUS); also elsewhere on the board
VDD_3V3_SPECKTRUM_EN: Pix1.19 (vdd_3V3_SPECTRUM_EN); also elsewhere on the board
VDD_5V_IN_PROT: Pix1.61 (VDD_5V_IN), Pix1.63 (VDD_5V_IN); also elsewhere on the board
VDD_SERVO_IN: Pix1.9 (VDD_SERVO_IN); also elsewhere on the board
~EXTERN_CS: Pix1.5 (~EXTERN_CS)
~FMU-LED_AMBER: Pix1.2 (~FMU-LED_AMBER)
~IO-LED_SAFETY_PROT: Pix1.28 (~IO-LED_SAFETY_PROT); also elsewhere on the board
~VBUS_VALID: Pix1.59 (~VBUS_VALID); also elsewhere on the board
~VDD_5V_PERIPH_EN: Pix1.27 (~VDD_5V_PERIPH_EN); also elsewhere on the board
~VDD_5V_PERIPH_OC: Pix1.43 (~VDD_5V_PERIPH_OC); also elsewhere on the board
~VDD_BACKUP_VALID: Pix1.57 (~VDD_BACKUP_VALID); also elsewhere on the board
~VDD_BRICK_VALID: Pix1.55 (~VDD_BRICK_VALID); also elsewhere on the board
~VDD_HIPOWER_OC: Pix1.45 (~VDD_5V_HIPOWER_OC); also elsewhere on the board

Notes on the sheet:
Some netlabels were removed because they will not be connected and the DRC was whining about them.


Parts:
C1, C6: 0.1uF; C_1206_3216Metric; Meta_Part CAP CER 0.1UF 50V 1206
C2, C5: 1nF; C_1206_3216Metric; Meta_Part CAP CER 1NF 50V 1206
C3, C4: 1uF; C_1206_3216Metric; Meta_Part CAP CER 1UF 50V 1206
F1, F2: 1A; Fuse_1206_3216Metric_Pad1.42x1.75mm_HandSolder; Meta_Part FUSE SMD 1A 60VDC 1206
U1, U2: LTC7000EMSE#PBF; SOP50P490X110-17N; Meta_Part LTC7000EMSE#PBF

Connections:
+BATT: F1.1, F2.2, U1.1 (RUN), U1.15 (SNS-), U1.16 (SNS+), U2.1 (RUN), U2.15 (SNS-), U2.16 (SNS+); also elsewhere on the board
GND: C2.2, C3.2, C4.2, C5.2, U1.4 (VCCUV), U1.8 (OVLO), U1.17 (GND), U2.4 (VCCUV), U2.8 (OVLO), U2.17 (GND); also elsewhere on the board
MOSFET_Driver_1_PG: U1.5 (~FAULT~); also elsewhere on the board
MOSFET_Driver_2_PG: U2.5 (~FAULT~); also elsewhere on the board
MOSFET_Driver_Enable: U1.7 (INP), U2.7 (INP); also elsewhere on the board
unnamed: C1.1, U1.14 (BST)
unnamed: C2.1, U1.6 (TIMER)
unnamed: C3.1, U1.3 (VCC)
unnamed: C4.1, U2.3 (VCC)
unnamed: C5.1, U2.6 (TIMER)
unnamed: C6.1, U2.14 (BST)
unnamed: F1.2, U1.2 (VIN)
unnamed: F2.1, U2.2 (VIN)
V+ESC: C1.2, C6.2, U1.13 (TS), U2.13 (TS); also elsewhere on the board
Vg_1: U1.11 (TGDN), U1.12 (TGUP); also elsewhere on the board
Vg_2: U2.11 (TGDN), U2.12 (TGUP); also elsewhere on the board

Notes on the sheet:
Current Sense disabled, using hall effect sensors elsewhere. SNS+ & SNS - must be above 1.5V.
TS acts as ref for boot- straping supply (BST)
To NMOS gate, TGUP & TGDN are gate pull up & pull down paths.
Voltage divider for UVLO & OVLO removed


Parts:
BUZZ1: Buzzer; BUZZER; Meta_Part Piezo buzzer
C15, C16, C17, C18, C19, C20, C21, C22, C23, C28, C29, C30, C32, C41, C42: EMI_Filter_C; FIL_NFM21HC224R1A3D; Meta_Part NFM21HC224R1A3D
CAN_GPS_1, CAN_GPS_2: Conn_01x04_Female; JST_GH_SM04B-GHS-TB_1x04-1MP_P1.25mm_Horizontal; Meta_Part JST-GH 4POS HEADER HORZ
GPS1: Conn_01x08_Female; JST_GH_BM08B-GHS-TBT_1x08-1MP_P1.25mm_Vertical; Meta_Part JST-GH 8POS HEADER VERT
GPS2: Conn_01x06_Female; JST_GH_BM06B-GHS-TBT_1x06-1MP_P1.25mm_Vertical; Meta_Part JST-GH 6POS HEADER VERT
HereLink1: Conn_01x09_Female; JST_GH_SM09B-GHS-TB_1x09-1MP_P1.25mm_Horizontal; Meta_Part JST-GH 9POS HEADER HORZ
J5: Conn_01x02_Female; BUZZ_CONN; Meta_Part DNP
J7, J11: Conn_01x02_Female; Molex_CLIK-Mate_502386-0270_1x02-1MP_P1.25mm_Horizontal; Meta_Part CLIK-Mate 1.25mm 2POS HORZ
J8, J9, J10: Conn_01x04_Female; Molex_CLIK-Mate_502382-0470_1x04-1MP_P1.25mm_Vertical; Meta_Part CLIK-Mate 1.25mm 4POS VERT
J21, J23, J39, J41: Conn_01x04_Female; JST_GH_BM04B-GHS-TBT_1x04-1MP_P1.25mm_Vertical; Meta_Part JST-GH 4POS HEADER VERT
J22: Conn_01x04_Female; JST_GH_SM04B-GHS-TB_1x04-1MP_P1.25mm_Horizontal; Meta_Part JST-GH 4POS HEADER HORZ
MOT_1, MOT_2, MOT_3, MOT_4, MOT_5, MOT_6, MOT_7, MOT_8: Conn_01x07_Female; JST_GH_SM07B-GHS-TB_1x07-1MP_P1.25mm_Horizontal; Meta_Part JST-GH 7POS HEADER HORZ
RFD_900x1: Conn_02x08_Odd_Even; RFD900_2x08_2.54mm; Meta_Part HEADER-F 0.1\" 2x8 POS THT
SERIAL1, SERIAL2: Conn_01x06_Female; JST_GH_BM06B-GHS-TBT_1x06-1MP_P1.25mm_Vertical; Meta_Part JST-GH 6POS HEADER VERT
SERIAL5: Conn_01x04_Female; JST_GH_BM04B-GHS-TBT_1x04-1MP_P1.25mm_Vertical; Meta_Part JST-GH 4POS HEADER VERT
USB0: Conn_01x04_Female; JST_GH_BM04B-GHS-TBT_1x04-1MP_P1.25mm_Vertical; Meta_Part JST-GH 4POS HEADER VERT

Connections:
5V3_Primary: C28.3; also elsewhere on the board
5V3_secondary: C32.3; also elsewhere on the board
5V_PERIPH_PRIMARY: C15.1, C16.1, C17.1, C20.1, C22.1, C29.3; also elsewhere on the board
5V_PERIPH_SECONDARY: C18.1, C19.1, C21.1, C23.1, C30.3, C41.1, C42.1; also elsewhere on the board
BUZZER: J5.2; also elsewhere on the board
CAN_1+: CAN_GPS_1.2, J21.2, J39.2; also elsewhere on the board
CAN_1-: CAN_GPS_1.3, J21.3, J39.3; also elsewhere on the board
CAN_2+: CAN_GPS_2.2, J22.2, J41.2; also elsewhere on the board
CAN_2-: CAN_GPS_2.3, J22.3, J41.3; also elsewhere on the board
CAN_3+: J23.2; also elsewhere on the board
CAN_3-: J23.3; also elsewhere on the board
GND: C15.2, C16.2, C17.2, C18.2, C19.2, C20.2, C21.2, C22.2, C23.2, C28.2, C29.2, C30.2, C32.2, C41.2, C42.2, CAN_GPS_1.4, CAN_GPS_2.4, GPS1.8, GPS2.6, HereLink1.2, HereLink1.4, HereLink1.6, HereLink1.8, J5.1, J7.1, J8.1, J8.2, J9.1, J9.2, J10.1, J10.2, J11.1, J21.4, J22.4, J23.4, J39.4, J41.4, MOT_1.1, MOT_1.7, MOT_2.1, MOT_2.7, MOT_3.1, MOT_3.7, MOT_4.1, MOT_4.7, MOT_5.1, MOT_5.7, MOT_6.1, MOT_6.7, MOT_7.1, MOT_7.7, MOT_8.1, MOT_8.7, RFD_900x1.1, RFD_900x1.2, RFD_900x1.16, SERIAL1.6, SERIAL2.6, SERIAL5.1, USB0.1; also elsewhere on the board
I2C_1_SCL: GPS1.4; also elsewhere on the board
I2C_1_SDA: GPS1.5; also elsewhere on the board
I2C_2_SCL: GPS2.4; also elsewhere on the board
I2C_2_SDA: GPS2.5; also elsewhere on the board
IO-CH1-PROT: MOT_1.5; also elsewhere on the board
IO-CH2-PROT: MOT_2.5; also elsewhere on the board
IO-CH3-PROT: MOT_3.5; also elsewhere on the board
IO-CH4-PROT: MOT_4.5; also elsewhere on the board
IO-CH5-PROT: MOT_5.5; also elsewhere on the board
IO-CH6-PROT: MOT_6.5; also elsewhere on the board
IO-CH7-PROT: MOT_7.5; also elsewhere on the board
IO-CH8-PROT: MOT_8.5; also elsewhere on the board
MOT-1_RPM: MOT_1.4; also elsewhere on the board
MOT-1_Rx: MOT_1.2; also elsewhere on the board
MOT-1_Tx: MOT_1.3; also elsewhere on the board
MOT-2_RPM: MOT_2.4; also elsewhere on the board
MOT-2_Rx: MOT_2.2; also elsewhere on the board
MOT-2_Tx: MOT_2.3; also elsewhere on the board
MOT-3_RPM: MOT_3.4; also elsewhere on the board
MOT-3_Rx: MOT_3.2; also elsewhere on the board
MOT-3_Tx: MOT_3.3; also elsewhere on the board
MOT-4_RPM: MOT_4.4; also elsewhere on the board
MOT-4_Rx: MOT_4.2; also elsewhere on the board
MOT-4_Tx: MOT_4.3; also elsewhere on the board
MOT-5_RPM: MOT_5.4; also elsewhere on the board
MOT-5_Rx: MOT_5.2; also elsewhere on the board
MOT-5_Tx: MOT_5.3; also elsewhere on the board
MOT-6_RPM: MOT_6.4; also elsewhere on the board
MOT-6_Rx: MOT_6.2; also elsewhere on the board
MOT-6_Tx: MOT_6.3; also elsewhere on the board
MOT-7_RPM: MOT_7.4; also elsewhere on the board
MOT-7_Rx: MOT_7.2; also elsewhere on the board
MOT-7_Tx: MOT_7.3; also elsewhere on the board
MOT-8_RPM: MOT_8.4; also elsewhere on the board
MOT-8_Rx: MOT_8.2; also elsewhere on the board
MOT-8_Tx: MOT_8.3; also elsewhere on the board
unnamed: C15.3, CAN_GPS_1.1
unnamed: C16.3, J39.1
unnamed: C17.3, J21.1
unnamed: C18.3, J22.1
unnamed: C19.3, J23.1
unnamed: C20.3, GPS1.1
unnamed: C21.3, GPS2.1
unnamed: C22.3, SERIAL1.1
unnamed: C23.3, SERIAL2.1
unnamed: C28.1, J9.3, J9.4
unnamed: C29.1, RFD_900x1.4
unnamed: C30.1, SERIAL5.4
unnamed: C32.1, J10.3, J10.4
unnamed: C41.3, CAN_GPS_2.1
unnamed: C42.3, J41.1
PPM-SBUS-PROT: HereLink1.7; also elsewhere on the board
PPM-SBUS-secondary: HereLink1.9; also elsewhere on the board
RFD_GPIO0: RFD_900x1.13; also elsewhere on the board
RFD_GPIO1: RFD_900x1.15; also elsewhere on the board
RFD_GPIO2: RFD_900x1.14; also elsewhere on the board
RFD_GPIO3: RFD_900x1.12; also elsewhere on the board
RFD_GPIO4: RFD_900x1.10
RFD_GPIO5: RFD_900x1.8
SAFETY: GPS1.6; also elsewhere on the board
SERAIL3_RX: GPS1.3; also elsewhere on the board
SERIAL1_CTS: RFD_900x1.11, SERIAL1.4; also elsewhere on the board
SERIAL1_RTS: RFD_900x1.3, SERIAL1.5; also elsewhere on the board
SERIAL1_RX: RFD_900x1.9, SERIAL1.3; also elsewhere on the board
SERIAL1_TX: RFD_900x1.7, SERIAL1.2; also elsewhere on the board
SERIAL2_CTS: SERIAL2.4; also elsewhere on the board
SERIAL2_RTS: SERIAL2.5; also elsewhere on the board
SERIAL2_RX: HereLink1.5, SERIAL2.3; also elsewhere on the board
SERIAL2_TX: HereLink1.3, SERIAL2.2; also elsewhere on the board
SERIAL3_TX: GPS1.2; also elsewhere on the board
SERIAL4_RX: GPS2.3; also elsewhere on the board
SERIAL4_TX: GPS2.2; also elsewhere on the board
SERIAL5_RX: SERIAL5.2; also elsewhere on the board
SERIAL5_TX: SERIAL5.3; also elsewhere on the board
STROBE: J7.2; also elsewhere on the board
USB_D+: USB0.3; also elsewhere on the board
USB_D-: USB0.2; also elsewhere on the board
VBUS: USB0.4; also elsewhere on the board
VDD_SERVO: HereLink1.1, J8.3, J8.4, J11.2, MOT_1.6, MOT_2.6, MOT_3.6, MOT_4.6, MOT_5.6, MOT_6.6, MOT_7.6, MOT_8.6; also elsewhere on the board
~IO-LED_SAFETY_PROT: GPS1.7; also elsewhere on the board

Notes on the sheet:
ESC Connectors
HereLink_Conn
CAN PORTS
GPS Default
GPS Secondary
RFD_900x Header
Serial 2
Serial 1
Legacy Pixhawk connectors
Telemetry Connections
Fan Header
Switchable Strobe Header
Auxiliary Power Headers
CUBE USB
Buzzer
Serial 5


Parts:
C24: 100uF; CP_Elec_10x10.5; Meta_Part CAP ALUM 100UF 20% 63V SMD
C25, C33: 10uF; C_1206_3216Metric; Meta_Part CAP CER 10UF 50V 1206
C26: 0.1uF; C_1206_3216Metric; Meta_Part CAP CER 0.1UF 50V 1206
C27: 22uF; C_1206_3216Metric; Meta_Part CAP CER 22UF 35V 1206
D12: LED_GREEN; LED_1206_3216Metric; Meta_Part LED SMD GREEN 1206
F5: 10A; Fuse_2512_6332Metric_Pad1.52x3.35mm_HandSolder; Meta_Part FUSE SMD 10A 60VDC 2-SMD
R1: 1k; R_1206_3216Metric; Meta_Part RES 1K OHM 1% 1/4W 1206
R2: 36k; R_1206_3216Metric; Meta_Part RES 36k OHM 1% 1/4W 1206
R3: 24k; R_1206_3216Metric; Meta_Part RES 24k OHM 1% 1/4W 1206
R6: 1.82K; R_1206_3216Metric; Meta_Part RES 1.82k OHM 1% 1/4W 1206
RV3: 1k; Potentiometer_Bourns_3266W_Vertical; Meta_Part 12 TURN TRIMMER 1K OHM 0.25W PC PIN TOP
U6: i3A4W005A150V; 1_32nd_Brick_8pin; Meta_Part i3A4W005A150V

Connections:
+BATT: F5.1; also elsewhere on the board
GND: C24.2, C25.2, C26.2, C27.2, C33.2, D12.1 (K), R3.2, R6.2, U6.3 (Vin(-)), U6.4 (Vout(-)); also elsewhere on the board
unnamed: C24.1, C25.1, C33.1, F5.2, U6.1 (Vin(+))
unnamed: D12.2 (A), R1.2
unnamed: R6.1, RV3.1
unnamed: RV3.2, U6.6 (TRIM)
Servo_Rail_PG: R2.2, R3.1, U6.5 (Power_Good); also elsewhere on the board
VDD_SERVO: C26.1, C27.1, R1.1, R2.1, U6.7 (SENSE(+)), U6.8 (Vout(+)); also elsewhere on the board
~Primary_Power_EN: U6.2 (ON/OFF); also elsewhere on the board

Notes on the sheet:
VDD_SERVO Supply - For powering Herelink, Fan, Servo...
See data sheet for layout and component selection guidelines, currently set for 12V output.
1.82K Resistance between TRIM and GND generates 12V OUT. Higher R = lower Vout


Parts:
C31, C35, C36, C38, C43, C44: 0.1uF; C_1206_3216Metric; Meta_Part CAP CER 0.1UF 50V 1206
C34: 1uF; C_1206_3216Metric; Meta_Part CAP CER 1UF 50V 1206
C37: 4.7uF; C_1206_3216Metric; Meta_Part CAP TANT 4.7UF 50V 1206
D10, D11: D_Schottky; D_0603_1608Metric_Castellated; Meta_Part Diode Schottky 0603 Vf < 450mV
F7: 1A; Fuse_1206_3216Metric_Pad1.42x1.75mm_HandSolder; Meta_Part FUSE SMD 1A 60VDC 1206
JP8, JP9, JP10, JP13: Jumper; SolderJumper-2_P1.3mm_Open_RoundedPad1.0x1.5mm; Meta_Part DNP
JP11, JP12: Jumper-DNP; SolderJumper-2_P1.3mm_Open_RoundedPad1.0x1.5mm; Meta_Part DNP
R7: 10k; R_1206_3216Metric; Meta_Part RES 10k OHM 1% 1/4W 1206
R8, R9: 24k; R_1206_3216Metric; Meta_Part RES 24k OHM 1% 1/4W 1206
R10, R11: 100k; R_1206_3216Metric; Meta_Part RES 100k OHM 1% 1/4W 1206
R12, R14: 150k; R_1206_3216Metric; Meta_Part RES 150k OHM 1% 1/4W 1206
R13, R15: 12k; R_1206_3216Metric; Meta_Part RES 12k OHM 1% 1/4W 1206
R16, R17: 47; R_1206_3216Metric; Meta_Part RES 47 OHM 1% 1/4W 1206
R18, R19: 270; R_1206_3216Metric; Meta_Part RES 270 OHM 1% 1/4W 1206
R20: 36k; R_1206_3216Metric; Meta_Part RES 36k OHM 1% 1/4W 1206
R21: 2k; R_1206_3216Metric; Meta_Part RES 2k OHM 1% 1/4W 1206
R29: 8.2k; R_1206_3216Metric; Meta_Part RES 8.2K OHM 1% 1/4W 1206
U7, U9, U10, U13: MCP601-xOT; SOT-23-5; Meta_Part MCP601-xOT
U8: TPS76350; SOT-23-5; Meta_Part TPS76350
U14: LM3480-3.3; SOT-23; Meta_Part Lin Reg 3.3V 0.1A 3-Pin SOT-23
U15: ACS71240LLCBTR-030B3; SOIC-8_3.9x4.9mm_P1.27mm; Meta_Part ACS71240LLCBTR-030B3

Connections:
5V3_OR'd: U14.2 (VI); also elsewhere on the board
5V3_Primary: F7.1; also elsewhere on the board
+3V3: C43.1, U14.1 (VO), U15.8 (VCC)
+5VA: C31.1, C37.1, R7.1, R12.2, R14.2, U7.5 (V+), U8.5 (VOUT), U9.5 (V+), U10.5 (V+), U13.5 (V+); also elsewhere on the board
+BATT: R20.1, U15.3 (IP-), U15.4 (IP-); also elsewhere on the board
ADC_IN: JP13.2; also elsewhere on the board
AUX_BATT_CURRENT_SENS: R17.1, R19.2; also elsewhere on the board
Aux_Hall: C44.1, R29.1; also elsewhere on the board
BATT_CURRENT_SENS_PROT: R16.1, R18.2; also elsewhere on the board
BATT_VOLTAGE_SENS_PROT: C38.1, R20.2, R21.1; also elsewhere on the board
Batt_Aux: U15.1 (IP+), U15.2 (IP+); also elsewhere on the board
GND: C31.2, C34.2, C37.2, C38.2, C43.2, C44.2, R10.1, R11.1, R18.1, R19.1, R21.2, U7.2 (V-), U8.2 (GND), U9.2 (V-), U10.2 (V-), U13.2 (V-), U14.3 (GND), U15.5 (GND); also elsewhere on the board
unnamed: C34.1, F7.2, U8.1 (VIN), U8.3 (EN)
unnamed: C35.1, R12.1, R13.1, U9.4 (-)
unnamed: C35.2, R13.2, R16.2, U9.1
unnamed: C36.1, R14.1, R15.1, U10.4 (-)
unnamed: C36.2, R15.2, R17.2, U10.1
unnamed: D10.1 (K), U7.1
unnamed: D10.2 (A), D11.2 (A), JP10.1, R7.2, U7.4 (-), U13.4 (-)
unnamed: D11.1 (K), U13.1
unnamed: JP8.2, U7.3 (+)
unnamed: JP9.2, U13.3 (+)
unnamed: JP10.2, JP11.1, JP12.1, JP13.1
unnamed: R8.2, R10.2, U9.3 (+)
unnamed: R9.2, R11.2, U10.3 (+)
unnamed: R29.2, U15.7 (VIOUT)
V1_Hall_raw: R8.1; also elsewhere on the board
V2_Hall_raw: R9.1; also elsewhere on the board
temp_A: JP8.1, JP11.2; also elsewhere on the board
temp_B: JP9.1, JP12.2; also elsewhere on the board

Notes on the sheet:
Diodes must have Vf lower than 450mV
Selects and forwards the lowest voltage form the temp sensor ICs (lower voltage = higher temperature so always reports worse case)
Verify current direction with bench test
Auxillary 30A current sensor
Signal Conditioning for Hall Sensor Output
5V LDO Regulator
3V3 LDO Regulator
Voltage Divider for Sensing Battery Voltage
PDB Tempature Sensor Selector
Jumpers allow bypass of selector cuircuit
Scales and buffers output of HALL effect current sensor from (approx) 0.5V - 4.5V --> 0.1V- 3.2V
The Hall current senor: ACS770ECB-200U-PFF-T is located on the seperate PDB board schematic. The V2_Hall_raw is connected directly to the output of the sensor. The sensor is powered by the same +5VA net on this page.

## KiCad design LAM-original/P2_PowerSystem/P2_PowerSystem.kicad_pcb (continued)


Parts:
C39, C40: 0.1uF; C_1206_3216Metric; Meta_Part CAP CER 0.1UF 50V 1206
D1: LED_GREEN; LED_1206_3216Metric; Meta_Part LED SMD GREEN 1206
D2, D3, D4, D5, D6, D7: LED_RED; LED_1206_3216Metric; Meta_Part LED SMD RED 1206
D8, D9: D; D_1206_3216Metric; Meta_Part Diode GEN PURP 1206
F8, F9: 500mA; Fuse_1206_3216Metric_Pad1.42x1.75mm_HandSolder; Meta_Part FUSE SMD 0.5A 10VDC 1206
J6: XT30PW-F; AMASS_XT30PW-F_1x02_P2.50mm_Horizontal; Meta_Part XT30PW-F
J15: Conn_01x05_Female; JST_GH_SM05B-GHS-TB_1x05-1MP_P1.25mm_Horizontal; Meta_Part JST-GH 5POS HEADER HORZ
J37, J38: Conn_02x20_Odd_Even; SAMTEC_SFC-120-T2-F-D-A; Meta_Part HEADER-F 0.05\" 2x20 POS SMD
JP1: Conn_02x06_Odd_Even; PinHeader_2x06_P1.27mm_Vertical; Meta_Part HEADER-F 0.05\" 2x6 POS THT
JP7, JP14: Jumper_3; PinHeader_1x03_P1.27mm_Vertical; Meta_Part HEADER-M 0.05\" 3 POS THT
R22: 270; R_1206_3216Metric; Meta_Part RES 270 OHM 1% 1/4W 1206
R23, R24, R25, R26, R27, R28: 500; R_1206_3216Metric; Meta_Part RES 500 OHM 1% 1/4W 1206
R30: 24k; R_1206_3216Metric; Meta_Part RES 24k OHM 1% 1/4W 1206
U11: 74HCT240; TSSOP-20_4.4x6.5mm_P0.65mm; Meta_Part 74HCT240
U12: SN74HC21-Q1; TSSOP-14_4.4x5mm_P0.65mm; Meta_Part SN74HC21-Q1

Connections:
5V3_OR'd: C39.1, C40.1, D8.1 (K), D9.1 (K), JP1.5, JP1.11, R30.2, U11.20 (VCC), U12.14 (Vcc); also elsewhere on the board
5V3_Primary: F9.1, J38.40; also elsewhere on the board
5V3_prime_PG: J37.28, U11.6 (1A2), U12.1 (1A); also elsewhere on the board
5V3_sec_PG: J37.30, U11.8 (1A3), U12.2 (1B); also elsewhere on the board
5V3_secondary: F8.1, J38.38; also elsewhere on the board
ADC_IN: J38.27; also elsewhere on the board
AUX_BATT_VOLTAGE_SENS: JP14.2 (C); also elsewhere on the board
Aux_Hall: J37.29, JP14.3 (B); also elsewhere on the board
Batt_Aux: J6.2; also elsewhere on the board
CAN_1+: J38.39; also elsewhere on the board
CAN_1-: J38.37; also elsewhere on the board
CAN_2+: J38.35; also elsewhere on the board
CAN_2-: J38.33; also elsewhere on the board
CAN_3+: J38.19; also elsewhere on the board
CAN_3-: J38.21; also elsewhere on the board
Ext_MOSFET_Driver_EN: J38.32, JP7.1 (A)
FMU-CH1-PROT: J37.12, JP1.6; also elsewhere on the board
FMU-CH2_PROT: J37.14; also elsewhere on the board
FMU-CH3_PROT: J37.16; also elsewhere on the board
FMU-CH4_PROT: J37.18; also elsewhere on the board
FMU-CH5_PROT: J37.20, JP1.1; also elsewhere on the board
FMU-CH6_PROT: J37.22, JP7.3 (B); also elsewhere on the board
GND: C39.2, C40.2, D1.1 (K), D2.1 (K), D3.1 (K), D4.1 (K), D5.1 (K), D6.1 (K), D7.1 (K), J6.1, J15.5, J37.25, J37.27, J38.1, J38.2, J38.17, JP1.3, JP1.7, U11.1 (1OE), U11.10 (GND), U11.19 (2OE), U12.7 (GND); also elsewhere on the board
I2C_1_SCL: J38.31; also elsewhere on the board
I2C_1_SDA: J38.29; also elsewhere on the board
I2C_2_SCL: J38.23; also elsewhere on the board
I2C_2_SDA: J38.25; also elsewhere on the board
I_MON_Payload: J15.2, J37.31, JP14.1 (A)
MOSFET_Driver_1_PG: J37.34, U11.15 (2A1), U12.5 (1D); also elsewhere on the board
MOSFET_Driver_2_PG: J37.36, U11.13 (2A2), U12.9 (2A); also elsewhere on the board
MOSFET_Driver_Enable: JP1.12, JP7.2 (C); also elsewhere on the board
MOT-1_RPM: J37.13; also elsewhere on the board
MOT-1_Rx: J37.17; also elsewhere on the board
MOT-1_Tx: J37.15; also elsewhere on the board
MOT-2_RPM: J38.20; also elsewhere on the board
MOT-2_Rx: J38.16; also elsewhere on the board
MOT-2_Tx: J38.18; also elsewhere on the board
MOT-3_RPM: J38.14; also elsewhere on the board
MOT-3_Rx: J38.10; also elsewhere on the board
MOT-3_Tx: J38.12; also elsewhere on the board
MOT-4_RPM: J37.19; also elsewhere on the board
MOT-4_Rx: J37.23; also elsewhere on the board
MOT-4_Tx: J37.21; also elsewhere on the board
MOT-5_RPM: J37.7; also elsewhere on the board
MOT-5_Rx: J37.11; also elsewhere on the board
MOT-5_Tx: J37.9; also elsewhere on the board
MOT-6_RPM: J38.26; also elsewhere on the board
MOT-6_Rx: J38.22; also elsewhere on the board
MOT-6_Tx: J38.24; also elsewhere on the board
MOT-7_RPM: J37.1; also elsewhere on the board
MOT-7_Rx: J37.5; also elsewhere on the board
MOT-7_Tx: J37.3; also elsewhere on the board
MOT-8_RPM: J38.8; also elsewhere on the board
MOT-8_Rx: J38.4; also elsewhere on the board
MOT-8_Tx: J38.6; also elsewhere on the board
unnamed: D1.2 (A), R22.2
unnamed: D2.2 (A), R23.2
unnamed: D3.2 (A), R24.2
unnamed: D4.2 (A), R25.2
unnamed: D5.2 (A), R26.2
unnamed: D6.2 (A), R27.2
unnamed: D7.2 (A), R28.2
unnamed: D8.2 (A), F9.2
unnamed: D9.2 (A), F8.2
unnamed: R23.1, U11.14 (1Y2)
unnamed: R24.1, U11.12 (1Y3)
unnamed: R25.1, U11.3 (2Y0)
unnamed: R26.1, U11.5 (2Y1)
unnamed: R27.1, U11.7 (2Y2)
unnamed: R28.1, U11.9 (2Y3)
unnamed: U11.4 (1A1), U12.8 (2Y)
unnamed: U11.2 (1A0), U11.16 (1Y1)
unnamed: U12.6 (1Y), U12.12 (2C), U12.13 (2D)
PPM-SBUS-PROT: J37.24; also elsewhere on the board
PPM-SBUS-secondary: J38.3; also elsewhere on the board
Payload_PG: J15.3, J37.32, R30.1, U11.17 (2A0), U12.4 (1C); also elsewhere on the board
RFD_GPIO0: J37.35; also elsewhere on the board
RFD_GPIO1: J37.39; also elsewhere on the board
RFD_GPIO2: J37.37; also elsewhere on the board
RFD_GPIO3: J37.33; also elsewhere on the board
S.BUS_OUT: J37.26; also elsewhere on the board
SERAIL3_RX: J38.7; also elsewhere on the board
SERIAL1_RX: J37.8; also elsewhere on the board
SERIAL1_TX: J37.10; also elsewhere on the board
SERIAL2_RX: J37.4; also elsewhere on the board
SERIAL2_TX: J37.6; also elsewhere on the board
SERIAL3_TX: J38.5; also elsewhere on the board
SERIAL4_RX: J38.11; also elsewhere on the board
SERIAL4_TX: J38.9; also elsewhere on the board
SERIAL5_RX: J38.15; also elsewhere on the board
SERIAL5_TX: J38.13; also elsewhere on the board
STROBE: JP1.10; also elsewhere on the board
Servo_Rail_PG: J37.38, U11.11 (2A3), U12.10 (2B); also elsewhere on the board
VDD_SERVO: JP1.9; also elsewhere on the board
Vout_payload: J15.1
temp_A: J38.34; also elsewhere on the board
temp_B: J38.36; also elsewhere on the board
~IO-LED_SAFETY_PROT: J37.2; also elsewhere on the board
~Payload_PW_EN: J15.4, J38.30, JP1.8
~Power_Fault: J37.40, JP1.2, R22.1, U11.18 (1Y0)
~Primary_Power_EN: J38.28, JP1.4; also elsewhere on the board

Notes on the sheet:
External Monitor Module Connection Headers
LED Indicators
Offboard Switches
Override to enable payload power supply, short terminals to enable.
Override to enable 5V3 power supplies,short terminals to enable.
Override to enable MOSFET Drivers, short terminals to enable.
Select between Autopilot control of MOSFET driver Enable and external monitor module control, leave both sides open when override is enabled
Power Monitoring Signals
Onboard Switches
Connect Power_Fault to Autopilot I/O
Oring both 5V3 supplies to create a redundant low current rail for monitoring circuits.
Master Power
MOSFET ENABLE
Strobe Enable
Payload PS Monitor
Aux batt Power Out
Power to strobe light
Future use for control pannel, could use for neopixel LED
These can either be confifured with jumpers on board, or conencted to a remote control pannel and controled there. The three pin jumpers should probubly be slightly seperated and not brought out to a pannel.
Jumpers / remote connenctor
EM_1
EM_2
Use aux battery input for optional current sensors instead


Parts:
C7, C11: 100uF; CP_Elec_10x10.5; Meta_Part CAP ALUM 100UF 20% 63V SMD
C8, C12, C45, C46: 10uF; C_1206_3216Metric; Meta_Part CAP CER 10UF 50V 1206
C9, C13: 0.1uF; C_1206_3216Metric; Meta_Part CAP CER 0.1UF 50V 1206
C10, C14: 22uF; C_1206_3216Metric; Meta_Part CAP CER 22UF 35V 1206
D13, D14: LED_GREEN; LED_1206_3216Metric; Meta_Part LED SMD GREEN 1206
F3, F4: 10A; Fuse_2512_6332Metric_Pad1.52x3.35mm_HandSolder; Meta_Part FUSE SMD 10A 60VDC 2-SMD
R4, R5: 8.2k; R_1206_3216Metric; Meta_Part RES 8.2K OHM 1% 1/4W 1206
R31, R33: 270; R_1206_3216Metric; Meta_Part RES 270 OHM 1% 1/4W 1206
R32, R34: 10k; R_1206_3216Metric; Meta_Part RES 10k OHM 1% 1/4W 1206
RV1, RV2: 1k; Potentiometer_Bourns_3266W_Vertical; Meta_Part 12 TURN TRIMMER 1K OHM 0.25W PC PIN TOP
U3, U5: i3A4W005A150V; 1_32nd_Brick_8pin; Meta_Part i3A4W005A150V
U4: Cube_PSM; PSM; Meta_Part Cube PSM

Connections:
3V3_Spectrum: U4.1 (VDD_3V3_SPEKTRUM)
5V3_Primary: C9.1, C10.1, R31.1, R32.2, U3.7 (SENSE(+)), U3.8 (Vout(+)), U4.24 (VDD_BRICK_IN); also elsewhere on the board
5V3_prime_PG: R32.1, U3.5 (Power_Good); also elsewhere on the board
5V3_sec_PG: R34.1, U5.5 (Power_Good); also elsewhere on the board
5V3_secondary: C13.1, C14.1, R33.1, R34.2, U4.22 (VDD_V_BACKUP), U5.7 (SENSE(+)), U5.8 (Vout(+)); also elsewhere on the board
5V_PERIPH_PRIMARY: U4.5 (VDD_5V_HIPOWER); also elsewhere on the board
5V_PERIPH_SECONDARY: U4.4 (VDD_5V_PERIPH); also elsewhere on the board
+BATT: F3.1, F4.1; also elsewhere on the board
ALARM: U4.12 (ALARM_fromCube); also elsewhere on the board
BUZZER: U4.13 (BUZZ_OUT); also elsewhere on the board
GND: C7.2, C8.2, C9.2, C10.2, C11.2, C12.2, C13.2, C14.2, C45.2, C46.2, D13.1 (K), D14.1 (K), R4.2, R5.2, U3.3 (Vin(-)), U3.4 (Vout(-)), U4.6 (GND), U5.3 (Vin(-)), U5.4 (Vout(-)); also elsewhere on the board
unnamed: C11.1, C12.1, C46.1, F4.2, U5.1 (Vin(+))
unnamed: C7.1, C8.1, C45.1, F3.2, U3.1 (Vin(+))
unnamed: D13.2 (A), R31.2
unnamed: D14.2 (A), R33.2
unnamed: R4.1, RV1.1
unnamed: R5.1, RV2.1
unnamed: RV1.2, U3.6 (TRIM)
unnamed: RV2.2, U5.6 (TRIM)
VBUS: U4.11 (VBUS_TO_FMU), U4.20 (VDD_VBUS); also elsewhere on the board
VDD_3V3_SPECKTRUM_EN: U4.9 (VDD_3V3_SPEKTRUM_EN); also elsewhere on the board
VDD_5V_IN_PROT: U4.15 (VDD_5V_TO_FMU); also elsewhere on the board
VDD_SERVO_IN: U4.19 (SERVO_IN); also elsewhere on the board
~Primary_Power_EN: U3.2 (ON/OFF), U5.2 (ON/OFF); also elsewhere on the board
~VBUS_VALID: U4.18 (~VBUS_VALID); also elsewhere on the board
~VDD_5V_PERIPH_EN: U4.10 (~VDD_5V_PERIPH_EN); also elsewhere on the board
~VDD_5V_PERIPH_OC: U4.8 (~VDD_5V_PERIPH_OC); also elsewhere on the board
~VDD_BACKUP_VALID: U4.17 (~VDD_BACKUP_VALID); also elsewhere on the board
~VDD_BRICK_VALID: U4.16 (~VDD_BRICK_VALID); also elsewhere on the board
~VDD_HIPOWER_OC: U4.7 (~VDD_5V_HI_POWER_OC); also elsewhere on the board

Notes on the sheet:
Direct to Cube Connections
8.57K Resistance between TRIM and GND generates 5V OUT. Higher R = lower Vout
Cube Primary 5.3V Supply
Cube Secondary 5.3V Supply



Board: 4 copper layers, 115.0 x 115.0 mm, 186 parts (19 on the bottom side), 189 nets.

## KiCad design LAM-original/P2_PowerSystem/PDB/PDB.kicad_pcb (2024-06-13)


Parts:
C1, C2: 0.1uF; C_1206_3216Metric_Pad1.42x1.75mm_HandSolder
C3, C4: 0.1uF; C_0603_1608Metric
J1, J2, J7, J8: Conn_01x01_Male; Pin_D1.3mm_L11.3mm_W2.8mm_Flat
J3, J4, J5, J6: Conn_02x03_Counter_Clockwise; PinHeader_2x03_P2.54mm_Vertical
J9, J10, J11, J12, J13, J14, J15, J16, J17, J18: Conn_01x02; XT-60_horizontal
J19, J20: Conn_01x02; AMASS_XT30PW-F_1x02_P2.50mm_Horizontal
J21, J22: Conn_01x01_Male; Wire_Pad_8x8mm
J23, J24: Conn_01x01_Male; MountingHole_4mm_Pad
Q1, Q2, Q3, Q4, Q5, Q6, Q7, Q8, Q9, Q10: IAUS300N08S5N012; Infineon_PG-HSOF-8-1; MPN IAUS300N08S5N012ATMA1
U1, U2: ACS770ECB-200U-PFF-T; CB-5_Formed_Leads; MPN ACS770ECB-200U-PFF-T
U3, U4: LMT87DCK; SOT-353_SC-70-5

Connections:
+5VA: C1.1, C2.1, C3.2, C4.2, J3.2, J5.2, U1.1 (VCC), U2.1 (VCC), U3.1 (Vdd), U3.4 (Vdd), U3.5 (Vdd), U4.1 (Vdd), U4.4 (Vdd), U4.5 (Vdd)
/Batt_RAW: J7.1, J8.1, U1.4 (IP+), U2.4 (IP+)
/V1_current: J5.3, U1.3 (VIOUT)
/V2_current: J3.3, U2.3 (VIOUT)
/V+_BATT: J3.1, J4.1, J4.2, J5.1, J6.1, J6.2, J19.2, J20.2, J21.1, J22.1, Q1.3 (D), Q2.3 (D), Q3.3 (D), Q4.3 (D), Q5.3 (D), Q6.3 (D), Q7.3 (D), Q8.3 (D), Q9.3 (D), Q10.3 (D), U1.5 (IP-), U2.5 (IP-)
/V+_ESC: J5.6, J6.6, J9.1, J10.1, J11.1, J12.1, J13.1, J14.1, J15.1, J16.1, J17.1, J18.1, Q1.2 (S), Q2.2 (S), Q3.2 (S), Q4.2 (S), Q5.2 (S), Q6.2 (S), Q7.2 (S), Q8.2 (S), Q9.2 (S), Q10.2 (S)
/Vg_1: J3.4, J6.4, Q1.1 (G), Q2.1 (G), Q3.1 (G), Q9.1 (G), Q10.1 (G)
/Vg_2: J4.4, J5.4, Q4.1 (G), Q5.1 (G), Q6.1 (G), Q7.1 (G), Q8.1 (G)
GND: C1.2, C2.2, C3.1, C4.1, J1.1, J2.1, J3.5, J3.6, J4.5, J4.6, J5.5, J6.5, J9.2, J10.2, J11.2, J12.2, J13.2, J14.2, J15.2, J16.2, J17.2, J18.2, J19.1, J20.1, J23.1, J24.1, U1.2 (GND), U2.2 (GND), U3.2 (GND), U4.2 (GND); also elsewhere on the board
temp_reading_A: J4.3, U3.3 (OUT)
temp_reading_B: J6.3, U4.3 (OUT)



Board: 2 copper layers, 115.0 x 115.0 mm, 46 parts (4 on the bottom side), 11 nets.

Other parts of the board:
M1, M2, M3, M4: MountingHole_3.2mm_M3_Pad

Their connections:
GND: M1.1, M2.1, M3.1, M4.1; also elsewhere on the board

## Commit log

2024-06-13 add simplified LAM PDB PCB
    [PDB.kicad_pcb, PDB.kicad_sch]
2024-06-13 add JLCPCB manufacturing files for simplified LAM PDB
    [PDB-CuBottom.gbr, PDB-CuTop.gbr, PDB-EdgeCuts.gbr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]
2024-06-13 add old LAM and SAM design files
    [0678H9150-02.step, 12V_SERVO_SUPPLY.sch, 18 SIZE CODE K16.stp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]
2024-06-17 add simplified SAM board schematics
    [AUX_Current_Monitor.kicad_sch, Autopilot_power_supply.kicad_sch, Connections.kicad_sch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]
2024-06-30 add production files for EasyLAM PDB, STEP for EasySAM
    [P2_PowerSystem.kicad_pcb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]
2024-07-01 EasySAM fix edge clearance violations
    [SAM4.kicad_pcb]
2024-11-27 add LED board production files
    [Lightboard BOM.xlsx, aerpaw_led_analysis.xlsx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]
2026-02-02 update LAM PDB PCB r1.3
    [PDB-CuBottom.gbr, PDB-CuTop.gbr, PDB-EdgeCuts.gbr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]
2026-02-02 add 3d AMASS conns
    [PDB.kicad_pcb, XT30PW-F.STEP, XT60PW-F.STEP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]
2026-02-03 fix XT90-F footprint
    [PDB.kicad_pcb]
2026-02-03 add BOM
    [PDB.kicad_sch]
2026-02-03 add 2.x revision for AS150 pdb pcbs
    [PDB.kicad_pcb, PDB.kicad_sch]
2026-02-03 add AS150U 3d+footprint
    [Amass AS150U Anti Spark Connector.stp]
2026-02-03 add AS150s to PDB r2.0
    [PDB.kicad_pcb, PDB.kicad_sch]
2026-02-05 add jlc manufacturing files
    [PDB-B_Cu.gbl, PDB-B_Mask.gbs, PDB-B_Paste.gbp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]
2026-02-27 add pcb raw image processing
2026-02-27 bring footprints to parity with modern kicad
    [aux_current_monitor.kicad_sch, connections.kicad_sch, cube_connection.kicad_sch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]
2026-02-27 reannotate sam schem to bring into parity
    [aux_current_monitor.kicad_sch, connections.kicad_sch, cube_psu.kicad_sch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]
2026-02-27 place top. revisit missing parts
    [connections.kicad_sch, esc_landing.kicad_sch, sam4.kicad_pcb]
2026-03-02 add WIP step file for sam boards
    [SAM4_Mainboard.step]
2026-03-04 finalize core routing
    [connections.kicad_sch, cube_psu.kicad_sch, esc_landing.kicad_sch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]
2026-03-09 add STEP file for r1.2 SAMe + SAM carrier and power delivery board
    [sam4_r1.2.step]
2026-03-10 add updated SAM4 routing (DRC clean) + model
    [Cube.STEP, aux_current_monitor.kicad_sch, aux_power.kicad_sch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]
2026-03-10 reorg directories
    [12V_SERVO_SUPPLY.sch, AUX_Current_Monitor.kicad_sch, AUX_Current_Monitor.sch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]
2026-03-18 final san check routing. add protection
    [aux_current_monitor.kicad_sch, aux_power.kicad_sch, connections.kicad_sch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]
2026-03-18 add JLC ordering files. small tweaks
    [aux_power.kicad_sch, cube_connection.kicad_sch, cube_psu.kicad_sch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]

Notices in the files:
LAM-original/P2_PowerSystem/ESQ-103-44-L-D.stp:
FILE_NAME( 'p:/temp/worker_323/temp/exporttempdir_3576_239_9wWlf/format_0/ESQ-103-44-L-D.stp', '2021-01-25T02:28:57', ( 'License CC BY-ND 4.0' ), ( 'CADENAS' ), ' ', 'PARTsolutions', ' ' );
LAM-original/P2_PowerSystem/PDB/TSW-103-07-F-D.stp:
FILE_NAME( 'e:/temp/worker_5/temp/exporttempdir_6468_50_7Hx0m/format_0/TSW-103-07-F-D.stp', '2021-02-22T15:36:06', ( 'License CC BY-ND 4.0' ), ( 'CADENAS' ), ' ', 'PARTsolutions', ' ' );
